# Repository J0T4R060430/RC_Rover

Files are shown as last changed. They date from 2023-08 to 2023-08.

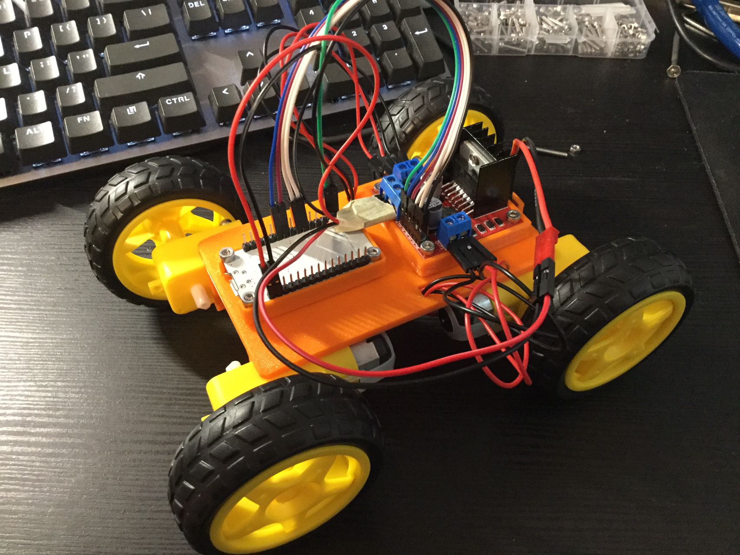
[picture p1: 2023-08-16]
Finished.jpg

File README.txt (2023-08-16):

Hello! Thank you for checking out my RC Rover project. I hope you will enjoy the building experience.

----------------------------------------------------------------------------
Contact Info:
email:   yihedai3@gmail.com
Github:  https://github.com/J0T4R060430
Youtube: https://www.youtube.com/channel/UCp56SjGfcEWq4QhWcSoFVbQ
----------------------------------------------------------------------------

Overview of the Project:
- You can find all the parts you need in the "Parts List.txt"
- You can find the instructions on how to 3D print, assemble the rover, and uploading the code in the "Instructions.docx"
- You can modify my design however you want
- You can use any of my stuff in your future design
- I learned a lot from this video: https://www.youtube.com/watch?v=FLNgkYBkLjA&t=190s
- Good luck and have fun!

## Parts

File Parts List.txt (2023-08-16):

Here is all of the parts I used for this project:
1. ESP32 Dev Kit
2. L293N Motor Driver
3. Arduino Driver Motor + Motor * 4
5. 7.4V 1800 mAh LiPo Battery
6. Deans T Plug
7. 10 FF Jumper Wires
8. 3D Printed Frame, ESP32 and L293N Driver Holder
9. Assorted M3 Screws:
	M3 * 25mm - 8
	M3 * 8mm - 8
	M3 * 6mm - 4
	M3 Hex Nut - 24
10. PS3 Controller

Amazon Purchase Links:
ESP32 - https://www.amazon.ca/dp/B07KTV2RRM?psc=1&ref=ppx_yo2ov_dt_b_product_details
Motors + Wheels + L293N - https://www.amazon.ca/dp/B0BLHTMSSP?psc=1&ref=ppx_yo2ov_dt_b_product_details
Battery - https://www.amazon.ca/dp/B0C38M7W2S?psc=1&ref=ppx_yo2ov_dt_b_product_details
Deans T Plug - https://www.amazon.ca/dp/B07FSPTPWL?psc=1&ref=ppx_yo2ov_dt_b_product_details

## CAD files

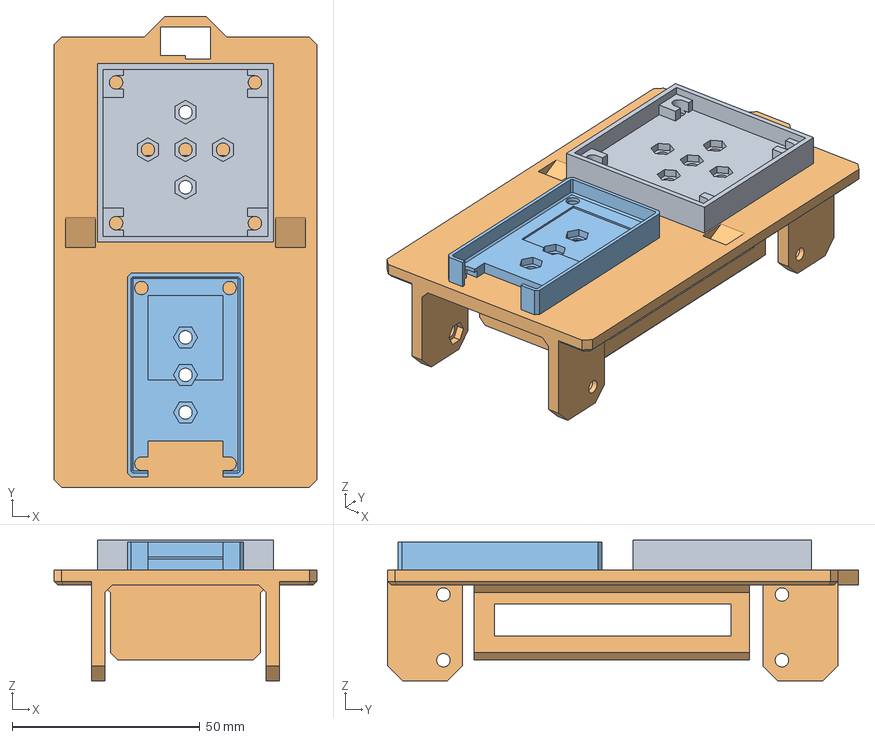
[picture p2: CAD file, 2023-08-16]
RC Rover Assembly V2 v6.3mf
70.0 x 125.5 x 37.5 mm
ESP32 Holder (1) (1) (1) (1)

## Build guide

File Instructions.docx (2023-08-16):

# RC Rover Instructions

Yee Dai


Part 1: Rover Assembly

Step 1:

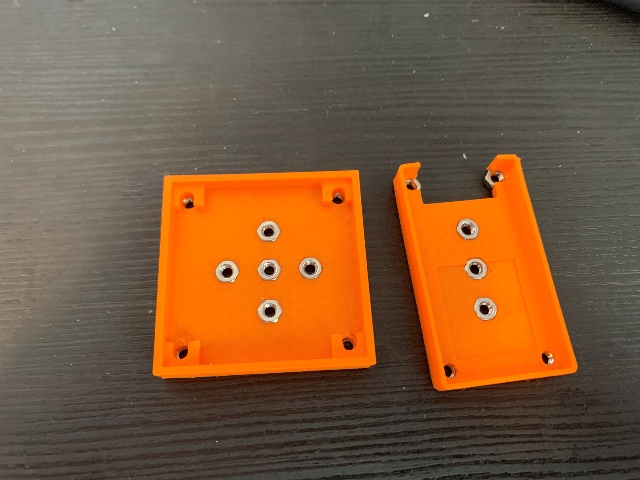
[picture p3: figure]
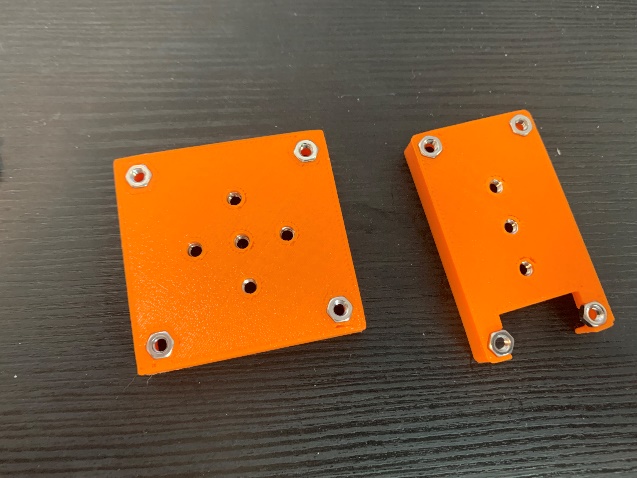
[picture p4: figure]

Insert M3 Hex Nut into all of the hexagon shaped holes on the 2 holders.

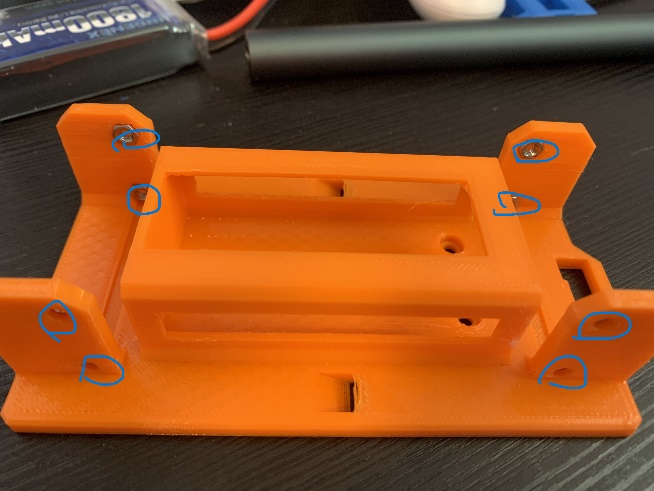
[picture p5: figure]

Insert M3 Hex Nut into all of the hexagon shaped holes on the Frame

Step 2:

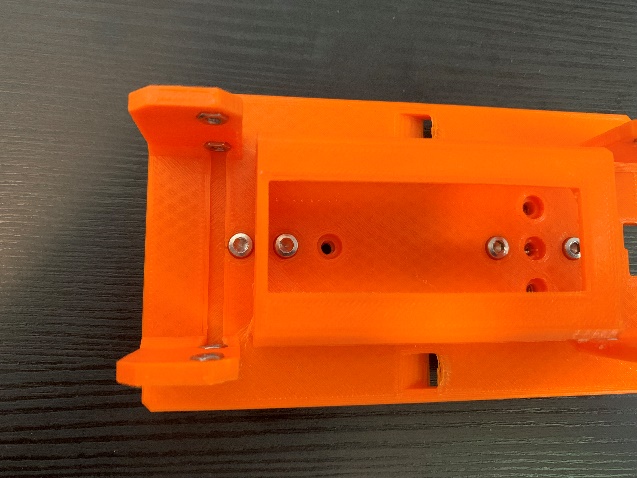
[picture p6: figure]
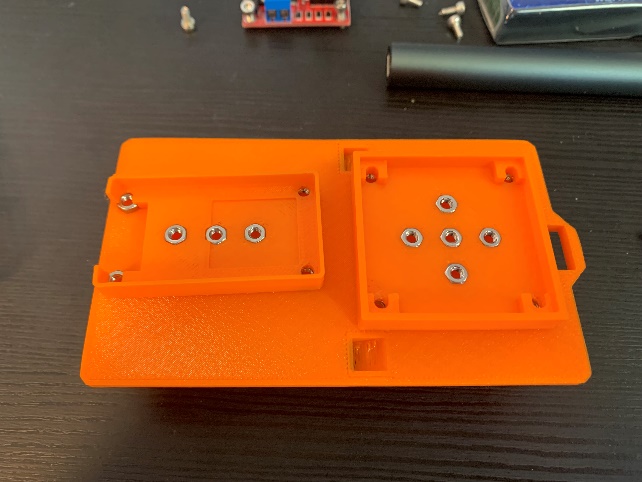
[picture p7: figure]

Use 4 M3*6 mm bolts to secure the 2 holders onto the frame. Be aware of the orientation.

Step 3:

Mount the ESP32 and L293N using 8 M3*8 mm bolts. Be aware of the orientation.

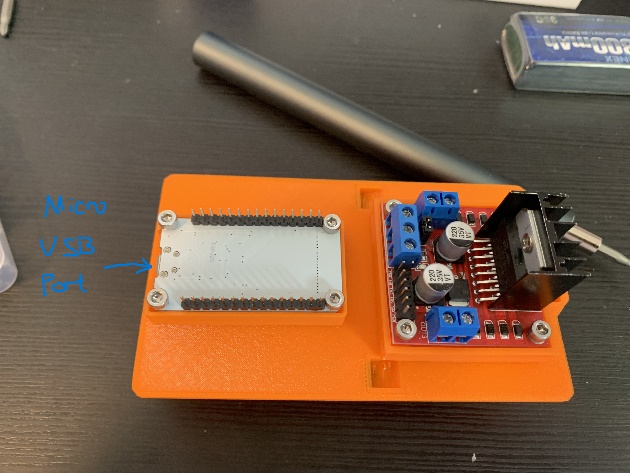
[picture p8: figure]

Slide in the Battery.

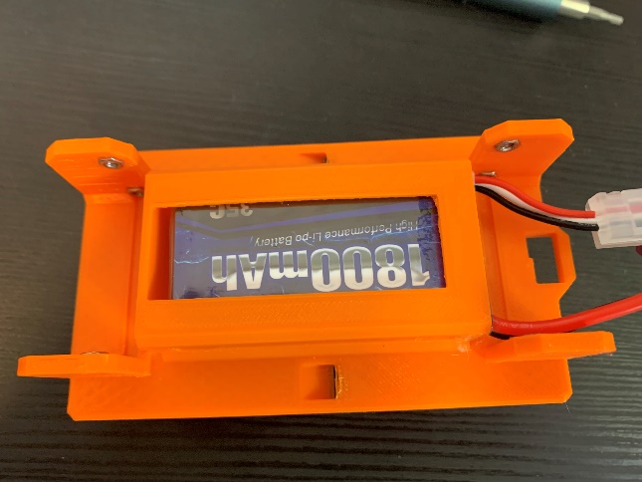
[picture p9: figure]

Step 4:

Connect the pins using Female to Female jumper wires as shown in the picture. This step is extremely important.

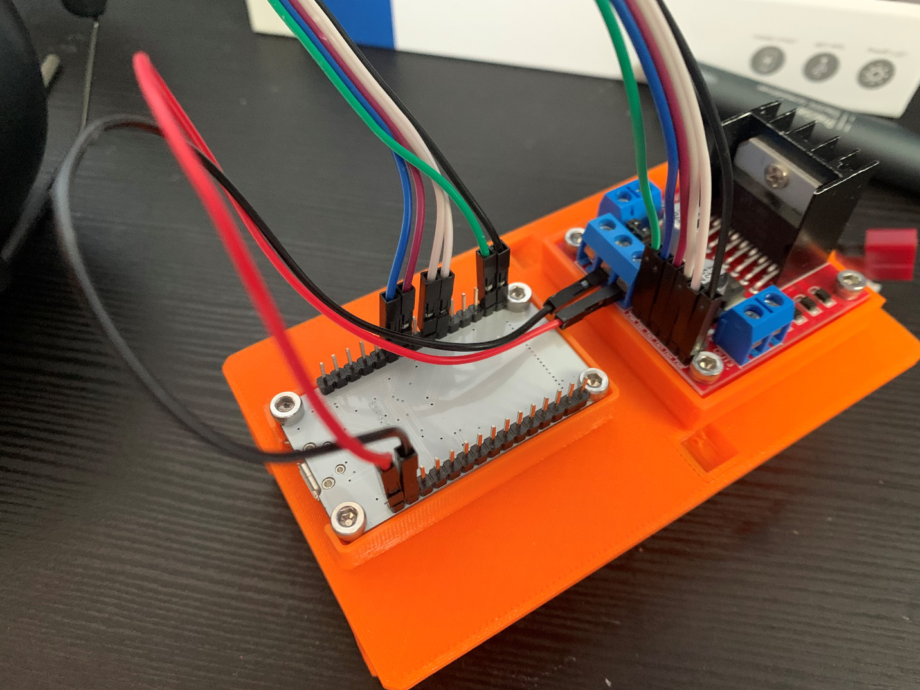
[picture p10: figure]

Step 5:

Connect the Deans T Plug wire to the L293N.

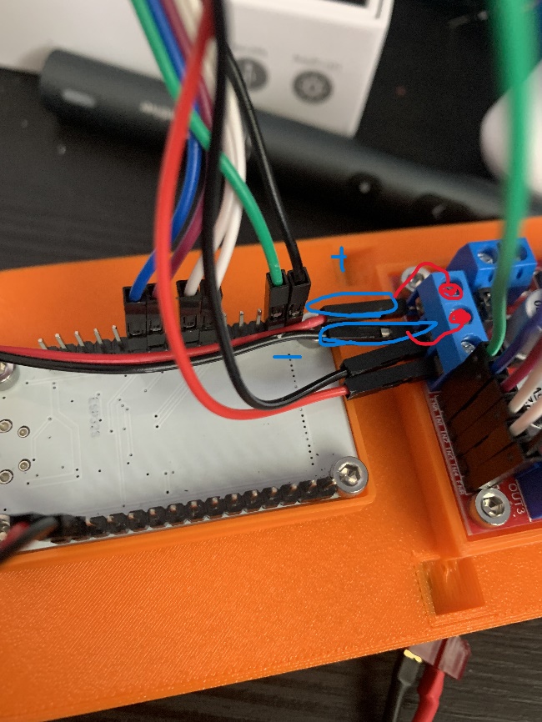
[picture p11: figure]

*FINAL WIRING SHOULD LOOK LIKE THIS:

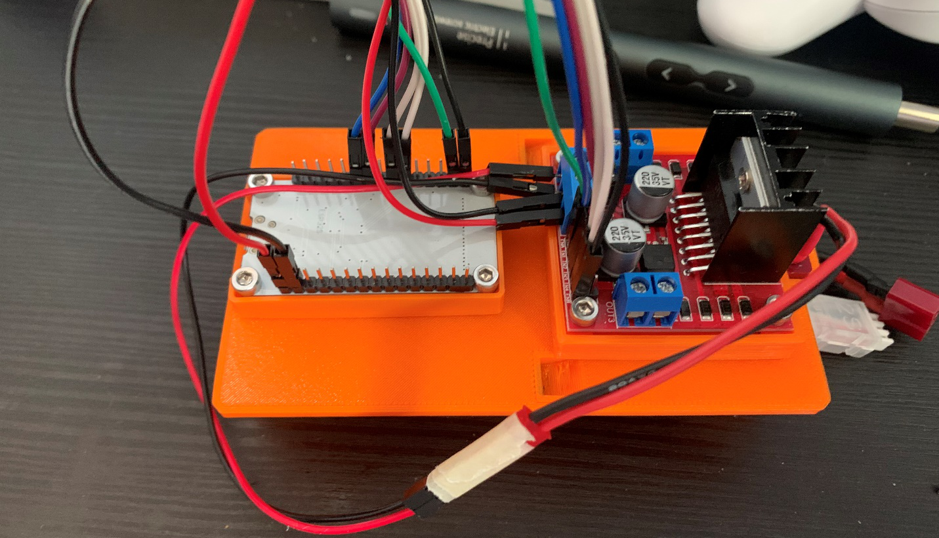
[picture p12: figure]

Step 6:

Use 8 M3 * 25 mm bolts to secure the driver motors to the frame. Make sure the soldered wiring part is pointed inside.

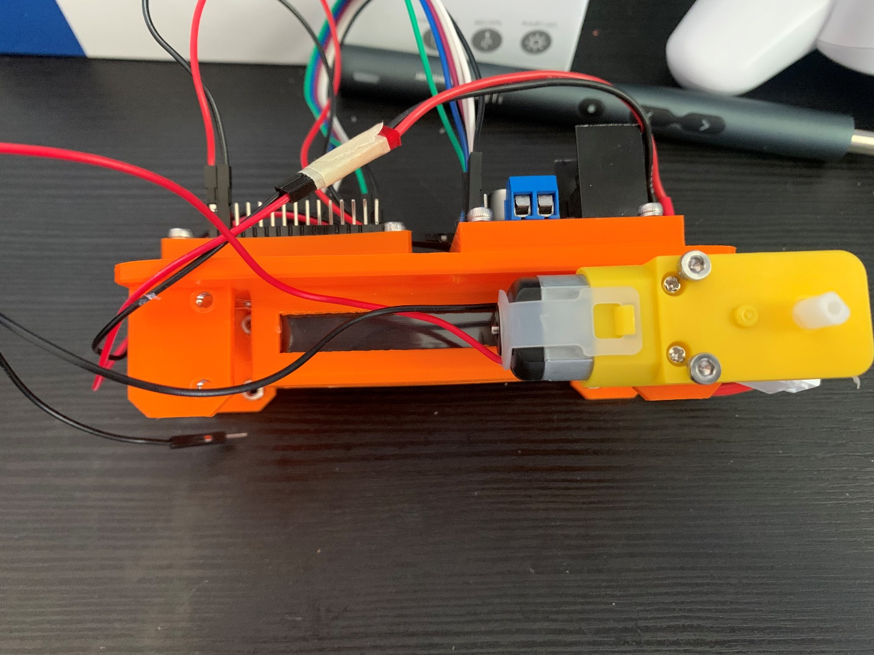
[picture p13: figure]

Step 7:

Feed the two power cables through the slanted hole on the side. Each hole should have 2 + and 2 – cables.

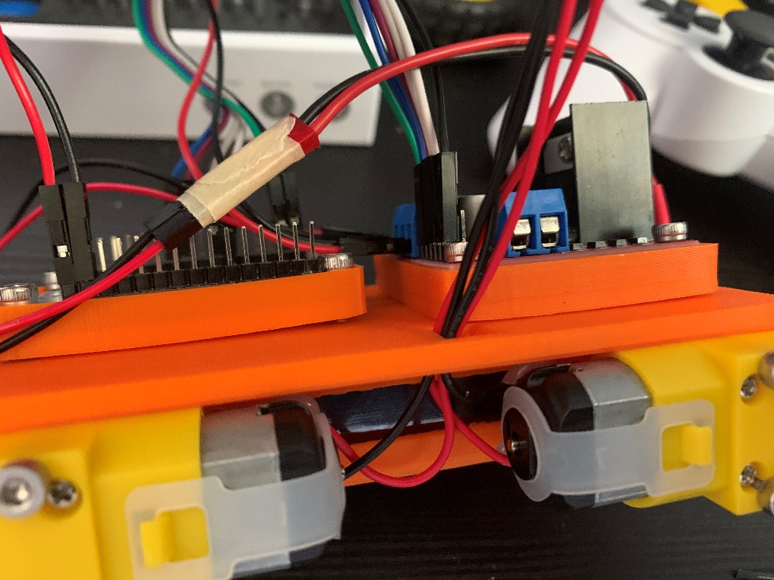
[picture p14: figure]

Step 8:

Connect the power cables as shown.

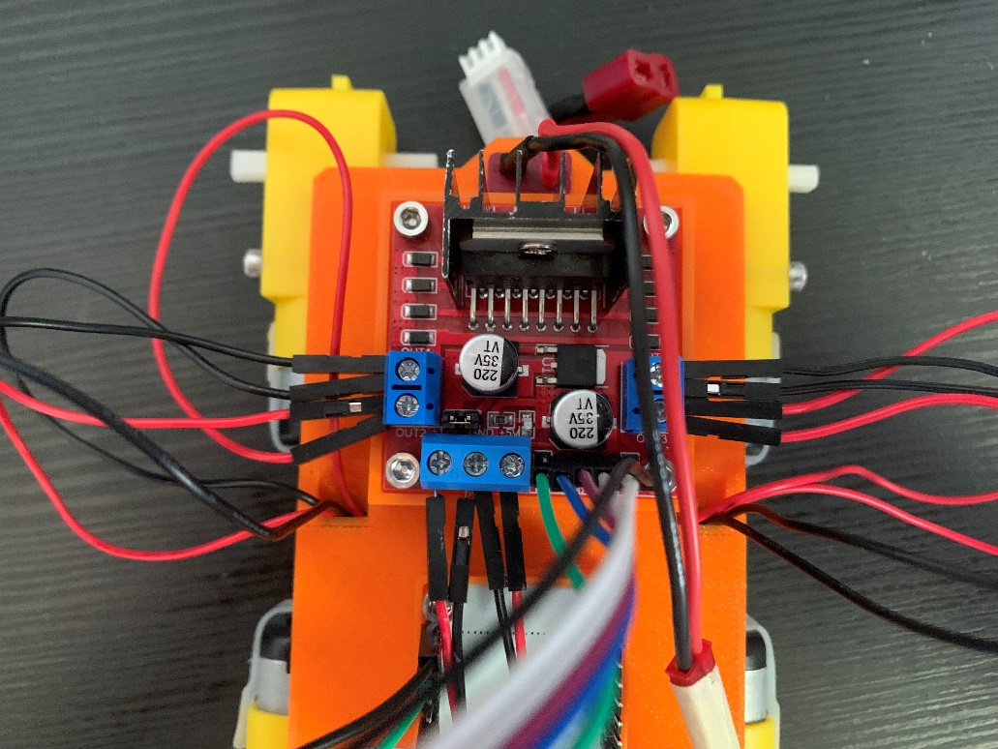
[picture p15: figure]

Step 9:

Connect the Power cables of the battery to the Deans T plug. Attach the wheels.

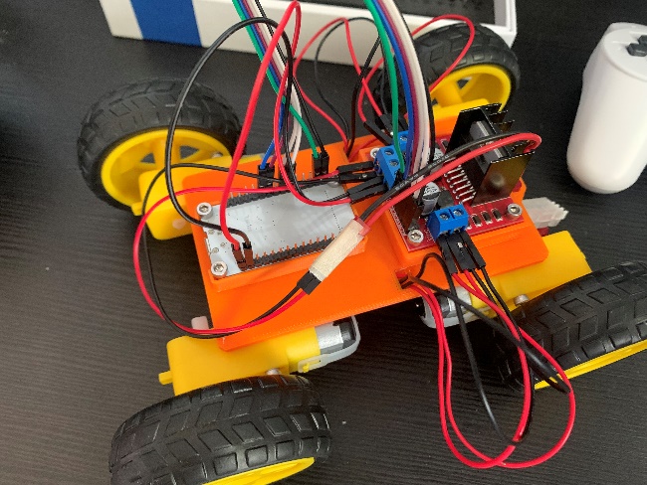
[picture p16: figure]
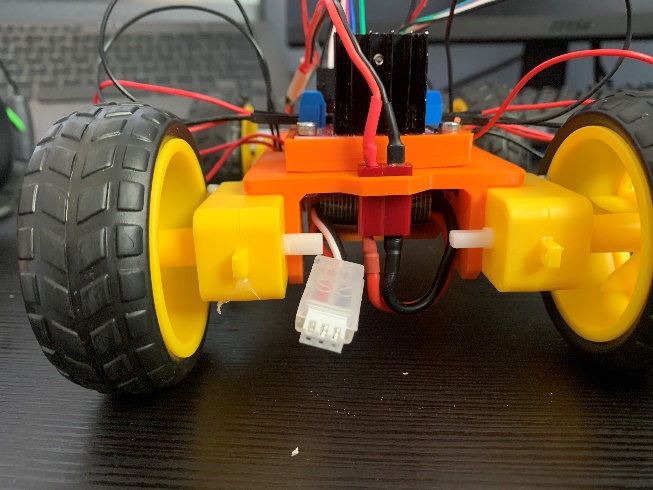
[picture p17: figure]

Part 2: Connect PS3 Controller

Follow this tutorial to connect PS3 Controller to ESP32:

https://www.youtube.com/watch?v=nctYJaDNLU0&t=1000s

if the above tutorial does not work, watch this one from 5:22 to 6:15:

https://www.youtube.com/watch?v=FLNgkYBkLjA&t=196s

Part 3: Upload Code:

Download AC_Car_OP.ino from Github. Make sure to insert your PS3 Controller MAC address between the quotation makes on line 114, and upload it onto your ESP32.

FINISHED

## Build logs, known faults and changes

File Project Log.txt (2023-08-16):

7/29/2023
-Started the project today. I tackled the bluetooth problem first.
-I watched some youtube videos on how to connect a PS3 controller to Arduino Uno R3, which I have on hand. I ordered a USB host shield and a bluetooth dongle, which will arrive tomorrow. Thank God for Amazon Prime.
-Here is what I want to do: Arduino Uno R3 at the bottom, USB host shield on top with bluetooth dongle connected to PS3 controller, and a motor shield on top, driving 4 dc motors. I will design and print the frame and wheels.
- Watched an hour of tutorials, L293N seems really good. I will order it with a 4 AA battery power supply. Its all working out.
-The final product will be a 4 wheel RC car controlled by PS3 controller.

7/30/2023
-L293N and bluetooth dongle came today, so I cant really work on anything. 
-Watched more Youtube tutorials, I think this will be quite easy

7/31/2023
-Everything arrived today. So excited.
-Shit Shit shit shittihi
-ok, so the bluetooth wont work, and the motor shield cannot do more than one motor at a time wwith 6v power supply
-The bluetooth part is so wacked, I correctly soldered the host shield, and tested it with a bunch of other appliances, so the USB host shield is fine
-the PS3 controller is definitely working because I was just using it for my emulator
-the Dongle! it sucks so much! i plugged it into my pc and it doesnt have the correct drivers!
-the motor shield is so dumb. the technology is so old - from 1960s, no wonder it requires 24V to power all 4 motors
-well something worked: my code. When I use a wired connection, Im getting input from the PS3, and the Arduino is sending signals to the motor shield, so one motor is running
-So tires, its 1 am, gonna sleep and deal with this mess tmr

8/1/2023
-OK, so I did tons more research, which is something I sould have done before making any purchases, and got solutions.
-I will replace the L293N with a Adafruit Motor Shield 2.0, which can power 4 6v DC motors with a 6V power supply. Also much better microprocessors cause its not made 60 years ago lol
-Still no solution to the Bluetooth problem, trying everything I can but still refuse to connect
-Ordered motor shield on Amazon. Ariiving on Saturday. Before that, I hope to fix the bluetooth Problem.

8/2/2023
-Did not Fix the Bluetooth. UUUUUUUUUUGGGGGGGGGGGGGGGGGGHHHHHHHHHHHHHHHHHHHHHHHHHH
-Really frustrated, decided to try PS4 controllers. One coming tmr.
-Something I did do today is make the prototype Arduino holder. Works not fine, will do more iterations tmr

8/3/2023
-Nope. PS4 does not work. I used the same knock off one in the tutorial but no connect. I am so mad rn
-Arduino Holder is finished now, it will slide in and be held by a m3.
-I have to figure out the bluetooth or this wont be a RC. Why did I not choose to use Radio?
-Started designing a mount for the 6v hobby motors. Making god progress.

8/4/2023
-Got a real Sony PS4 controller from facebook. Trying it out.
-Noooooooooooooooooooooooooooooooooooooooooooooooooooooo
-Yeah it didn't work, still no connect. Its probably the dongle, because everything else works except that.
-tested the dongle on Windows 10 System, works fine. What is the probelm? Searched forums for 2 hours and this problem seems prettty common, and no one has a reliable solution. Guess its a chance game.
-Ordered new Dongle, arrving tmr.
-Finished the first Version of the motor mount. Works ok, adding more grip tmr

8/5/2023
-I. Hate. Bluetooth. New dongle also no workie. returned immediately.
-Motor Mount is perfected. Uses hot glue to really secure it, and there are holes with nuts inside to connect it to main frame using M3 nuts.
-Motor Shield Arrived, tested it. Works like a charm, but now I'm seeing more problems.
-The 6V DC motors spin too fast for a wheel, and has like no torque. They are made for drones and boats after all. Gonna replace them in the future.
-Bluetooth refuses to work. Seeking alternatives.
-Found something. this WEMOS D1 R32 seems like a dream come true. It has built in Wifi and Buetooth, has 4 MB cache, and so much storage. Overall a great replacement for Arduino Uno. It's even build to mimic the arduino uno shape, so all the shields will work with it. Is this my salvation?
-And it runs Arduino Code! This could be it!

8/6/2023
-OK, HUGE progress! The godforsaken Bluetooth finally worked, although it only connects to the PS3... No matter, a connection is a connection. Im so grateful.
⠀⠀⠀⠀⠀⠀⠀⠀⠀⠀⠀⠀⠀⡟⠋⠈⠙⣦⠀⠀⠀⠀⠀⠀⠀⠀⠀⠀⠀⠀⠀⠀⠀⠀⠀⠀⠀⠀⠀⠀⣠⠤⢤⡀⠀⠀
⠀⠀⠀⠀⠀⠀⠀⠀⠀⠀⠀⠀⠀⡇⠀⠀⠀⠈⢇⠀⠀⠀⠀⠀⠀⠀⠀⠀⠀⠀⠀⠀⠀⠀⠀⠀⠀⠀⡠⠞⠀⠀⢠⡜⣦⠀
⠀⠀⠀⠀⠀⠀⠀⠀⠀⠀⠀⠀⠀⡃⠀⠀⠀⠀⠈⢷⡄⠀⠀⠀⠀⠀⠀⠀⠀⠀⠀⠀⠀⠀⠀⠀⡠⠊⣠⠀⠀⠀⠀⢻⡘⡇
⠀⠀⠀⠀⠀⠀⠀⠀⠀⠀⠀⠀⢠⠃⠀⠀⠀⠀⠀⠀⠙⢶⣀⡀⠀⠀⠀⠀⠀⠀⠀⠀⠀⢀⡠⠚⢀⡼⠃⠀⠀⠀⠀⠸⣇⢳
⠀⠀⠀⠀⠀⠀⠀⠀⠀⠀⠀⠀⣾⠀⣀⠖⠀⠀⠀⠀⠉⠀⠀⠈⠉⠛⠛⡛⢛⠛⢳⡶⠖⠋⠀⢠⡞⠀⠀⠀⠐⠆⠀⠀⣿⢸
⠀⠀⠀⠀⠀⠀⠀⠀⠀⠀⠀⣼⠇⠀⠀⠀⠀⠀⠀⠀⠀⠀⠀⠀⠀⠀⠀⠀⠀⠀⠀⠻⣦⣀⣴⡟⠀⠀⢶⣶⣾⡿⠀⠀⣿⢸
⠀⠀⠀⠀⠀⠀⠀⠀⢀⣤⠞⠁⠀⠀⠀⠀⠀⠀⠀⠀⡠⠀⠀⠀⠀⠀⠀⠀⠀⠀⠀⠀⠈⠻⣏⠀⠀⠀⣶⣿⣿⡇⠀⠀⢏⡞
⠀⠀⠀⠀⠀⠀⢀⡴⠛⠀⠀⠀⠀⠀⠀⠀⠀⢀⢀⡾⠁⠀⠀⠀⠀⠀⠀⠀⠀⠀⠀⠀⠀⠀⠘⢦⣤⣾⣿⣿⠋⠀⠀⡀⣾⠁
⠀⠀⠀⠀⠀⣠⠟⠁⠀⠀⠀⣀⠀⠀⠀⠀⢀⡟⠈⢀⣤⠂⠀⠀⠀⠀⠀⠀⠀⠀⠀⠀⠀⠀⠀⠀⠉⠙⣏⡁⠀⠐⠚⠃⣿⠀
⠀⠀⠀⠀⣴⠋⠀⠀⠀⡴⣿⣿⡟⣷⠀⠀⠊⠀⠴⠛⠁⠀⠀⠀⠀⠀⠀⠀⠀⠀⠀⠀⠀⠀⠀⠀⠀⠀⠀⠙⠀⠀⠀⠀⢹⡆
⠀⠀⠀⣴⠃⠀⠀⠀⠀⣇⣿⣿⣿⠃⠀⠀⠀⠀⠀⠀⠀⠀⢀⣤⡶⢶⣶⣄⡀⠀⠀⠀⠀⠀⠀⠀⠀⠀⠀⠀⠀⠀⠀⠀⠀⡇
⠀⠀⣸⠃⠀⠀⠀⢠⠀⠊⠛⠉⠁⠀⠀⠀⠀⠀⠀⠀⢲⣾⣿⡏⣾⣿⣿⣿⣿⠖⠀⠀⠀⠀⠀⠀⠀⠀⠀⠀⠀⠀⠀⠀⠀⢧
⠀⢠⡇⠀⠀⠀⠀⠈⠀⠀⠀⠀⠀⠀⠀⠀⠀⠀⠀⠀⠈⠈⠛⠿⣽⣿⡿⠏⠁⠀⠀⠀⠀⠀⠀⠀⠀⠀⠀⠀⠀⠀⠀⠀⠀⡜
⢀⡿⠀⠀⠀⠀⢀⣤⣶⣟⣶⣦⣄⡀⠀⠀⠀⠀⠀⠀⠀⠀⠀⠀⠀⠀⠀⠀⠀⠀⠀⠀⠀⠀⠀⠀⠀⠀⠀⠀⠀⠀⠀⠀⠀⡇
⢸⠇⠀⠀⠀⠀⣿⣿⣿⣿⣿⣿⣿⣿⣧⠀⠀⠀⠀⠀⠀⠀⠀⠀⠀⠀⠀⠀⠀⠀⠀⠀⠀⠀⠀⠀⠀⠀⠀⠀⠀⠀⠀⠀⠀⡇
⣼⠀⢀⡀⠀⠀⢷⣿⣿⣿⣿⣿⣿⡿⠁⠀⠀⠀⠀⠀⠀⠀⠀⠀⠀⠀⠀⠀⠀⠀⠀⠀⠀⠀⠀⠀⠀⠀⠀⠀⠀⠀⠀⠀⢠⡇
⡇⠀⠈⠀⠀⠀⣬⠻⣿⣿⣿⡿⠙⠀⠀⢀⠀⠀⠀⠀⠀⠀⠀⠀⠀⠀⠀⠀⠀⠀⠀⠀⠀⠀⠀⠀⠀⠀⠀⠀⠀⠀⠀⠀⣼⠁
⢹⡀⠀⠀⠀⠈⣿⣶⣿⣿⣝⡛⢳⠭⠍⠉⠀⠀⠀⠀⠀⠀⠀⠀⠀⠀⠀⠀⠀⠀⠀⠀⠀⠀⠀⠀⠀⠀⠀⠀⠀⠀⠀⢰⠃⠀
⠸⡇⠀⠀⠀⠀⠙⣿⣿⣿⣿⣿⣿⣷⣦⣀⣀⣀⣤⣤⣴⡶⠀⠀⠀⠀⠀⠀⠀⠀⠀⠀⠀⠀⠀⠀⠀⠀⠀⠀⠀⠀⣰⠇⠀⠀
⠀⢿⡄⠀⠀⠀⠀⠀⠙⣇⠉⠉⠙⠛⠻⠟⠛⠛⠉⠙⠉⠀⠀⠀⠀⠀⠀⠀⠀⠀⠀⠀⠀⠀⠀⠀⠀⠀⠀⠀⠀⡰⠋⠀⠀⠀
⠀⠈⢧⠀⠀⠀⠀⠀⠀⠈⠀⠀⠀⠀⠀⠀⠀⠀⠀⠀⠀⠀⠀⠀⠀⠀⠀⠀⠀⠀⠀⠀⠀⠀⠀⠀⠀⠀⠀⣠⠞⠁⠀⠀⠀⠀
⠀⠀⠘⢷⡀⠀⠀⠀⠀⠀⠀⠀⠀⠀⠀⠀⠀⠀⠀⠀⠀⠀⠀⠀⠀⠀⠀⠀⠀⠀⠀⠀⠀⠀⠀⠀⠀⣠⠞⠁⠀⠀⠀⠀⠀⠀
⠀⠀⠀⠀⠱⢆⠀⠀⠀⠀⠀⠀⠀⠀⠀⠀⠀⠀⠀⠀⠀⠀⠀⠀⠀⠀⠀⠀⠀⠀⠀⠀⠀⠀⣀⡴⠋⠁⠀⠀⠀⠀⠀⠀⠀⠀
⠀⠀⠀⠀⠀⠀⠛⢦⣀⡀⠀⠀⠀⠀⠀⠀⠀⠀⠀⠀⠀⠀⠀⠀⠀⠀⠀⠀⠀⠀⣀⣠⠴⠟⠁⠀⠀⠀⠀⠀⠀⠀⠀⠀⠀⠀
⠀⠀⠀⠀⠀⠀⠀⠀⠈⠛⠲⠤⣤⣤⣤⣄⠀⠀⠀⠀⠀⠀⠀⢠⣤⣤⠤⠴⠒⠛⠋⠀⠀⠀⠀⠀⠀⠀⠀⠀⠀⠀⠀⠀⠀⠀Happy Face
-Bad new. Motor Shield does not like the 3.3V on D1 R32. It refuses to talk with the board and doesn't work overall. Need fixing.
-Also Desgined the main frame. Printing a V1 for testing. 5 hours, not Bad.
-So I went around and did more digging... And found a gem. The ESP32. The D1 R32 uses it as a processor, so the same performance and functions, but it deosn't rely on the arduino ecosystem. ESP32 is so much more robust than Arduino, and it workes great with this L293N Motor Driver that I have been eyeing for a while. Gonna give it a try.
-Also found lots of amazing tutorials from this channel on Youtube: https://www.youtube.com/@hashincludeelectronics. Absolutely Amazing stuff. He used ESP32, L293N, and PS controllers to make a lot of interesting stuff, which includes my project as well. Why didn't I just follow the tutorials? Could've saved so Much trouble. Stupid.

8/7/2023
-ESP32 is so good. Everything works flawlessly. Connects to PS3 faster than anything else, and the range is amazing. Thank God for SixAxis Pair tool, absolute life saver, being able to change the MAC address is so important.
-I think I jinxed myself. I need a 7-12V power supply for the ESP32 and 2 Motor ports to be powerd at the same time, and preferably stronger than AA batteries. Decided to order a 7.4V LiPo Battery. Also ordered jumper wires, Deans Plug, and Actual wheels and more suitable motors.
-Worked on code a lot. Copy Pasted like 200 lines of code today. I want my RC to drive like a tank, one joyStick for one side.
-Code is done and tested, and it is 2 AM. Yawn.

8/8/2023
-Wheels arrived, waiting for battery. In theory everythign should work, so Im not stressed.
-Started designing the holder for ESP32 and L293N. Finished before Lunch.
-Started designing new motor mounts, and this one is relatively easy. Managed to perfect it before Dinner.
-Started designing the main frame, 2.0. Although I don't have the physical battery, I did find its dimensions online. 
-The main frame looks liek this: A flat board with cutouts for the components, and 4 motor mounts printed on instead of attached. ESP32 on top and in front, L293N close behind. Holes for wires to go through. Looks really solid, starting a print before bed.

8/9/2023
-Checked print, everything fits perfectly except for the hole reserved for the Deans T plug to stay in. Used Soldering iron to melt away aprt of plastic, now works.
-Assembled everything. Looking really nice. The RC is very compact, 180mm long and 85mm wide, 60 mm tall.
-Code is loaded, just waiting for Battery.
-Shit, Battery is slightly bigger than the dimesntions given online, so it doesn'y fit.
-Made final adjsutments to main frame, will get final print around 9 pm.
-It is 8:30. So nervous.
-Moment of truth---
-It fits!
-AAAAAAAAAAAHHHHHHHHHHHHHHHHHHHHHHHHHHHHHHHHHHHHHHHHHHHHHHHHHHHHHH
⠀⠀⠀⠀⠀⠀⠀⠀⠀⠀⠀⠀⠀⡟⠋⠈⠙⣦⠀⠀⠀⠀⠀⠀⠀⠀⠀⠀⠀⠀⠀⠀⠀⠀⠀⠀⠀⠀⠀⠀⣠⠤⢤⡀⠀⠀
⠀⠀⠀⠀⠀⠀⠀⠀⠀⠀⠀⠀⠀⡇⠀⠀⠀⠈⢇⠀⠀⠀⠀⠀⠀⠀⠀⠀⠀⠀⠀⠀⠀⠀⠀⠀⠀⠀⡠⠞⠀⠀⢠⡜⣦⠀
⠀⠀⠀⠀⠀⠀⠀⠀⠀⠀⠀⠀⠀⡃⠀⠀⠀⠀⠈⢷⡄⠀⠀⠀⠀⠀⠀⠀⠀⠀⠀⠀⠀⠀⠀⠀⡠⠊⣠⠀⠀⠀⠀⢻⡘⡇
⠀⠀⠀⠀⠀⠀⠀⠀⠀⠀⠀⠀⢠⠃⠀⠀⠀⠀⠀⠀⠙⢶⣀⡀⠀⠀⠀⠀⠀⠀⠀⠀⠀⢀⡠⠚⢀⡼⠃⠀⠀⠀⠀⠸⣇⢳
⠀⠀⠀⠀⠀⠀⠀⠀⠀⠀⠀⠀⣾⠀⣀⠖⠀⠀⠀⠀⠉⠀⠀⠈⠉⠛⠛⡛⢛⠛⢳⡶⠖⠋⠀⢠⡞⠀⠀⠀⠐⠆⠀⠀⣿⢸
⠀⠀⠀⠀⠀⠀⠀⠀⠀⠀⠀⣼⠇⠀⠀⠀⠀⠀⠀⠀⠀⠀⠀⠀⠀⠀⠀⠀⠀⠀⠀⠻⣦⣀⣴⡟⠀⠀⢶⣶⣾⡿⠀⠀⣿⢸
⠀⠀⠀⠀⠀⠀⠀⠀⢀⣤⠞⠁⠀⠀⠀⠀⠀⠀⠀⠀⡠⠀⠀⠀⠀⠀⠀⠀⠀⠀⠀⠀⠈⠻⣏⠀⠀⠀⣶⣿⣿⡇⠀⠀⢏⡞
⠀⠀⠀⠀⠀⠀⢀⡴⠛⠀⠀⠀⠀⠀⠀⠀⠀⢀⢀⡾⠁⠀⠀⠀⠀⠀⠀⠀⠀⠀⠀⠀⠀⠀⠘⢦⣤⣾⣿⣿⠋⠀⠀⡀⣾⠁
⠀⠀⠀⠀⠀⣠⠟⠁⠀⠀⠀⣀⠀⠀⠀⠀⢀⡟⠈⢀⣤⠂⠀⠀⠀⠀⠀⠀⠀⠀⠀⠀⠀⠀⠀⠀⠉⠙⣏⡁⠀⠐⠚⠃⣿⠀
⠀⠀⠀⠀⣴⠋⠀⠀⠀⡴⣿⣿⡟⣷⠀⠀⠊⠀⠴⠛⠁⠀⠀⠀⠀⠀⠀⠀⠀⠀⠀⠀⠀⠀⠀⠀⠀⠀⠀⠙⠀⠀⠀⠀⢹⡆
⠀⠀⠀⣴⠃⠀⠀⠀⠀⣇⣿⣿⣿⠃⠀⠀⠀⠀⠀⠀⠀⠀⢀⣤⡶⢶⣶⣄⡀⠀⠀⠀⠀⠀⠀⠀⠀⠀⠀⠀⠀⠀⠀⠀⠀⡇
⠀⠀⣸⠃⠀⠀⠀⢠⠀⠊⠛⠉⠁⠀⠀⠀⠀⠀⠀⠀⢲⣾⣿⡏⣾⣿⣿⣿⣿⠖⠀⠀⠀⠀⠀⠀⠀⠀⠀⠀⠀⠀⠀⠀⠀⢧
⠀⢠⡇⠀⠀⠀⠀⠈⠀⠀⠀⠀⠀⠀⠀⠀⠀⠀⠀⠀⠈⠈⠛⠿⣽⣿⡿⠏⠁⠀⠀⠀⠀⠀⠀⠀⠀⠀⠀⠀⠀⠀⠀⠀⠀⡜
⢀⡿⠀⠀⠀⠀⢀⣤⣶⣟⣶⣦⣄⡀⠀⠀⠀⠀⠀⠀⠀⠀⠀⠀⠀⠀⠀⠀⠀⠀⠀⠀⠀⠀⠀⠀⠀⠀⠀⠀⠀⠀⠀⠀⠀⡇
⢸⠇⠀⠀⠀⠀⣿⣿⣿⣿⣿⣿⣿⣿⣧⠀⠀⠀⠀⠀⠀⠀⠀⠀⠀⠀⠀⠀⠀⠀⠀⠀⠀⠀⠀⠀⠀⠀⠀⠀⠀⠀⠀⠀⠀⡇
⣼⠀⢀⡀⠀⠀⢷⣿⣿⣿⣿⣿⣿⡿⠁⠀⠀⠀⠀⠀⠀⠀⠀⠀⠀⠀⠀⠀⠀⠀⠀⠀⠀⠀⠀⠀⠀⠀⠀⠀⠀⠀⠀⠀⢠⡇
⡇⠀⠈⠀⠀⠀⣬⠻⣿⣿⣿⡿⠙⠀⠀⢀⠀⠀⠀⠀⠀⠀⠀⠀⠀⠀⠀⠀⠀⠀⠀⠀⠀⠀⠀⠀⠀⠀⠀⠀⠀⠀⠀⠀⣼⠁
⢹⡀⠀⠀⠀⠈⣿⣶⣿⣿⣝⡛⢳⠭⠍⠉⠀⠀⠀⠀⠀⠀⠀⠀⠀⠀⠀⠀⠀⠀⠀⠀⠀⠀⠀⠀⠀⠀⠀⠀⠀⠀⠀⢰⠃⠀
⠸⡇⠀⠀⠀⠀⠙⣿⣿⣿⣿⣿⣿⣷⣦⣀⣀⣀⣤⣤⣴⡶⠀⠀⠀⠀⠀⠀⠀⠀⠀⠀⠀⠀⠀⠀⠀⠀⠀⠀⠀⠀⣰⠇⠀⠀
⠀⢿⡄⠀⠀⠀⠀⠀⠙⣇⠉⠉⠙⠛⠻⠟⠛⠛⠉⠙⠉⠀⠀⠀⠀⠀⠀⠀⠀⠀⠀⠀⠀⠀⠀⠀⠀⠀⠀⠀⠀⡰⠋⠀⠀⠀
⠀⠈⢧⠀⠀⠀⠀⠀⠀⠈⠀⠀⠀⠀⠀⠀⠀⠀⠀⠀⠀⠀⠀⠀⠀⠀⠀⠀⠀⠀⠀⠀⠀⠀⠀⠀⠀⠀⠀⣠⠞⠁⠀⠀⠀⠀
⠀⠀⠘⢷⡀⠀⠀⠀⠀⠀⠀⠀⠀⠀⠀⠀⠀⠀⠀⠀⠀⠀⠀⠀⠀⠀⠀⠀⠀⠀⠀⠀⠀⠀⠀⠀⠀⣠⠞⠁⠀⠀⠀⠀⠀⠀
⠀⠀⠀⠀⠱⢆⠀⠀⠀⠀⠀⠀⠀⠀⠀⠀⠀⠀⠀⠀⠀⠀⠀⠀⠀⠀⠀⠀⠀⠀⠀⠀⠀⠀⣀⡴⠋⠁⠀⠀⠀⠀⠀⠀⠀⠀
⠀⠀⠀⠀⠀⠀⠛⢦⣀⡀⠀⠀⠀⠀⠀⠀⠀⠀⠀⠀⠀⠀⠀⠀⠀⠀⠀⠀⠀⠀⣀⣠⠴⠟⠁⠀⠀⠀⠀⠀⠀⠀⠀⠀⠀⠀
⠀⠀⠀⠀⠀⠀⠀⠀⠈⠛⠲⠤⣤⣤⣤⣄⠀⠀⠀⠀⠀⠀⠀⢠⣤⣤⠤⠴⠒⠛⠋⠀⠀⠀⠀⠀⠀⠀⠀⠀⠀⠀⠀⠀⠀⠀Another very Happy face :D
-RC Car is finished. Runs better than expected, got some pretty solid batteries.
-PROJECT FINISHED!!!!!!!!!!!!!!!!!!!!!!!!!!!!!!

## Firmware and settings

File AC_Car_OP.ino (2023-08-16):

#include <Ps3Controller.h>

//Right motor
int enableRightMotor=22; 
int rightMotorPin1=16;
int rightMotorPin2=17;
//Left motor
int enableLeftMotor=23;
int leftMotorPin1=18;
int leftMotorPin2=19;

int rSpeed = 0;
int lSpeed = 0;

bool doubleSpeed = false;

#define MAX_MOTOR_SPEED 200

const int PWMFreq = 1000; /* 1 KHz */
const int PWMResolution = 8;
const int rightPWMSpeedChannel = 4;
const int leftPWMSpeedChannel = 5;

// void notify()
// {
//   int yAxisValue =(Ps3.data.analog.stick.ly);  //Left stick  - y axis - forward/backward car movement
//   int xAxisValue =(Ps3.data.analog.stick.rx);  //Right stick - x axis - left/right car movement

//   if (yAxisValue <= -50)       //Move car Forward
//   {
//     rotateMotor(MAX_MOTOR_SPEED, MAX_MOTOR_SPEED);
//   }
//   else if (yAxisValue >= 50)   //Move car Backward
//   {
//     rotateMotor(-MAX_MOTOR_SPEED, -MAX_MOTOR_SPEED);
//   }
//   else if (xAxisValue >= 50)  //Move car Right
//   {
//     rotateMotor(-MAX_MOTOR_SPEED, MAX_MOTOR_SPEED);
//   }
//   else if (xAxisValue <= -50)   //Move car Left
//   {
//     rotateMotor(MAX_MOTOR_SPEED, -MAX_MOTOR_SPEED);
//   }
//   else                                      //Stop the car
//   {
//     rotateMotor(0, 0);
//   } 
// }


void drive(){
  if(Ps3.data.analog.stick.ry < -20 || Ps3.data.analog.stick.ry > 20){
    rSpeed = map(Ps3.data.analog.stick.ry, -127, 127, -100, 100);
  }else{
    rSpeed = 0;
  }
  if(Ps3.data.analog.stick.ly < -20 || Ps3.data.analog.stick.ly > 20){
    lSpeed = map(Ps3.data.analog.stick.ly, -127, 127, -100, 100);
  }else{
    lSpeed = 0;
  }
  if(Ps3.event.button_down.r2){
    doubleSpeed = true;
  }
  if(Ps3.event.button_up.r2){
    doubleSpeed = false;
  }
  if(doubleSpeed){
    rSpeed *= 2; lSpeed *= 2;
  }
  Serial.print(lSpeed);
  Serial.print("    ");
  Serial.println(rSpeed);
  rotateMotor(rSpeed, lSpeed);
}

void rotateMotor(int rightMotorSpeed, int leftMotorSpeed)
{
  if (rightMotorSpeed < 0)
  {
    digitalWrite(rightMotorPin1,LOW);
    digitalWrite(rightMotorPin2,HIGH);    
  }
  else if (rightMotorSpeed > 0)
  {
    digitalWrite(rightMotorPin1,HIGH);
    digitalWrite(rightMotorPin2,LOW);      
  }
  else
  {
    digitalWrite(rightMotorPin1,LOW);
    digitalWrite(rightMotorPin2,LOW);      
  }
  
  if (leftMotorSpeed < 0)
  {
    digitalWrite(leftMotorPin1,LOW);
    digitalWrite(leftMotorPin2,HIGH);    
  }
  else if (leftMotorSpeed > 0)
  {
    digitalWrite(leftMotorPin1,HIGH);
    digitalWrite(leftMotorPin2,LOW);      
  }
  else
  {
    digitalWrite(leftMotorPin1,LOW);
    digitalWrite(leftMotorPin2,LOW);      
  }  
  ledcWrite(rightPWMSpeedChannel,abs(rightMotorSpeed));
  ledcWrite(leftPWMSpeedChannel, abs(leftMotorSpeed));
}

void setUpPinModes()
{
  pinMode(enableRightMotor,OUTPUT);
  pinMode(rightMotorPin1,OUTPUT);
  pinMode(rightMotorPin2,OUTPUT);
  
  pinMode(enableLeftMotor,OUTPUT);
  pinMode(leftMotorPin1,OUTPUT);
  pinMode(leftMotorPin2,OUTPUT);

  //Set up PWM for motor speed
  ledcSetup(rightPWMSpeedChannel, PWMFreq, PWMResolution);
  ledcSetup(leftPWMSpeedChannel, PWMFreq, PWMResolution);
  ledcAttachPin(enableRightMotor, rightPWMSpeedChannel);
  ledcAttachPin(enableLeftMotor, leftPWMSpeedChannel);  
  
  rotateMotor(0, 0);
}


void setup()
{
  setUpPinModes();
  Serial.begin(115200);
  Ps3.attach(drive);
  Ps3.begin("c0:49:ef:91:c6:82");
  Serial.println("Ready.");
}

void loop()
{
}
